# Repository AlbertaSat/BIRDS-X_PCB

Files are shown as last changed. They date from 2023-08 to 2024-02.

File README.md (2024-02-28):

# JASPER BIRDS-X PCB
Repository for the PCB design for the JASPER BIRDS-X project.

JASPER is a joint organization between the University of Alberta's AlbertaSat and the University of Calgary's CalgaryToSpace cubesat teams.

## Features
1. Capable of APRS (Automated Packet Reporting System) digipeat and store-and-forward modes, and periodic beaconing, for use by Amateur Radio enthusiasts.
2. Implements a radiation experiment, which compares the radiation shielding properties of shielding options.
	* Uses RADFET sensors as radiation detection sensors.
	* Uses linear CCD sensor (painted black) to sense galactic cosmic rays.
3. Employs power safety systems (over-current protection, enable pins, etc.) to interface with the BIRDS-X satellite parent system.
4. Uses <300 mW on receive, and <1750 mW on transmit.
5. ~~Stores data in flash memory.~~
6. Interfaces with the Mission Boss system via UART.
7. A test fixture board makes flashing and debugging the main payload board easier and more reliable.

## System Block Diagram

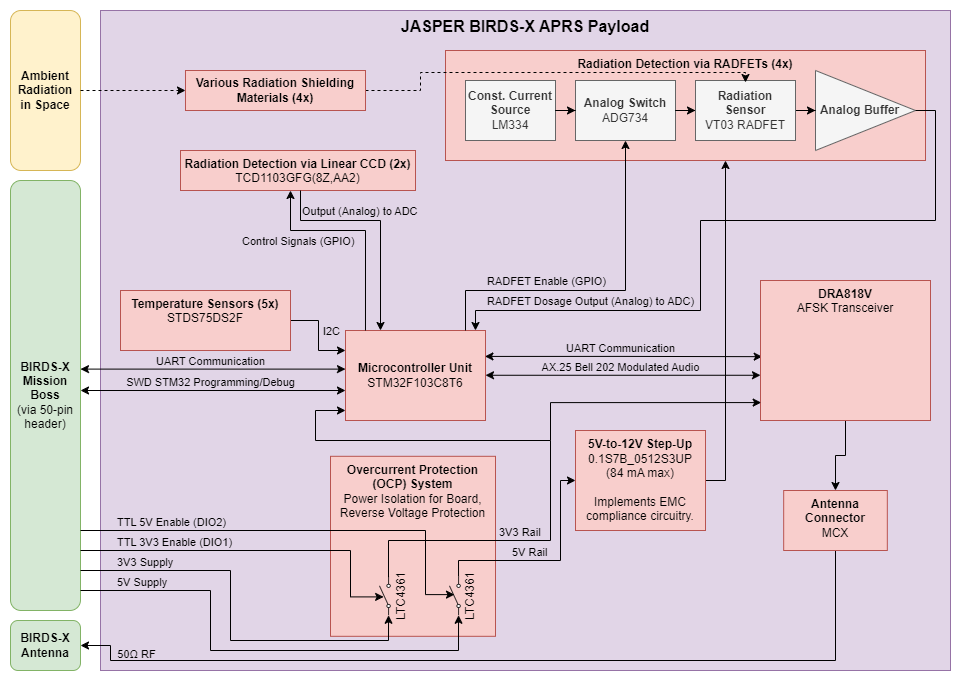
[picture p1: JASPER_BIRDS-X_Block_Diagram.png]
JASPER BIRDS-X Block Diagram


## Release Notes
See the [GitHub Releases](https://github.com/AlbertaSat/BIRDS-X_PCB/releases) for this repo.

## License

This repository is licensed under the "CERN Open Hardware Licence Version 2 - Permissive (CERN OHL v2 Permissive)" license. For more information, see [the choosealicense.com description of the license](https://choosealicense.com/licenses/cern-ohl-p-2.0/).

> CERN OHL v2 Permissive
> A permissive license for hardware designs, with conditions only requiring preservation of notices. Contributors provide an express grant of patent rights. Licensed works, modifications, and larger works may be distributed under different terms and without sources.

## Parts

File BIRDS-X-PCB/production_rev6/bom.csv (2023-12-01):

Designator | Footprint | Quantity | Value | LCSC Part #
C201, C202, C601, C701 | 0603 | 4 | 10u
C203, C204 | 0603 | 2 | 1u
C205, C206, C302 | 0603 | 3 | 4.7u
C208 | 0603 | 1 | 2.2u
C301, C303, C304, C305, C401, C402, C404, C405, C406, C407, C501, C502, C503, C504, C505 | 0603 | 15 | 100n
C403 | 0603 | 1 | 10n
C602, C603, C702, C703 | 0603 | 4 | 0.1u
C604, C605, C704, C705 | 0603 | 4 | 0.01u
D201, D202, D203, D301, D304, D_RX301, D_TX301 | 0603 | 7 | LED | C93128
D302, D303 | 0603 | 2 | LED | C375577
D801, D802, D901, D902 | D_DO-35_SOD27_P7.62mm_Horizontal | 4 | 1N457
H101, H102, H103, H104 | MountingHole_3.8mm | 4 | MountingHole
H105 | AlbertaSat_Logo_25x20mm | 1 | Logo
H106 | CTS_Logo_50x25mm | 1 | Logo
IC601, IC701 | TCD1103GFG8ZAA2 | 2 | TCD1103GFG_8Z,AA2_
J101, J102, J103 | Laird_Technologies_BMI-S-101_13.66x12.70mm | 3 | RFShield_OnePiece
J104 | PinHeader_2x25_P2.00mm_Horizontal | 1 | LPC-50M2LG
J401 | SMA_Amphenol_901-143_Horizontal_Modified | 1 | 60611002111501
JP201 | SolderJumper-2_P1.3mm_Open_RoundedPad1.0x1.5mm | 1 | Jumper_2_Open
L201 | 0603 | 1 | 6.8uH
Q201, Q202 | SOT-23 | 2 | 2N7002 | C3290044
Q203, Q204 | SOT-23 | 2 | AO3420
Q401 | SOT-23 | 1 | BC847 | C475630
Q601, Q701 | SOT-23 | 2 | 2SA1015 | C5189099
R201, R202, R802, R804, R902, R904 | 0603 | 6 | 110k
R203 | 1206 | 1 | 0.51 | C104948
R204 | 1206 | 1 | 0.075 | C171394
R205, R501, R502 | 0603 | 3 | 3k3
R206 | 0603 | 1 | 5.1k
R207 | 0603 | 1 | 51k
R301, R302, R305, R306, R309, R310, R602, R702 | 0603 | 8 | 2k2
R401, R404 | 0603 | 2 | 470
R402 | 0603 | 1 | 10k
R403, R805, R806, R807, R808, R905, R906, R907, R908 | 0603 | 9 | 0
R405, R408 | 1206 | 2 | 10k
R407, R410, R411 | 0603 | 3 | 100k
R412 | 0603 | 1 | 22k
R601, R603, R701, R703 | 0603 | 4 | 150
R801, R803, R901, R903 | 0603 | 4 | 11k
R809, R811, R909, R911 | 0603 | 4 | 10M
R810, R812, R910, R912 | 0603 | 4 | 3.6M
TP201, TP202 | TestPoint_Pad_D1.5mm | 2 | TestPoint
U201, U202 | TSOT-23-8_HandSoldering | 2 | LTC4361-2
U203 | Converter_DCDC_Gaptec_0.1S7B_3UP_THT | 1 | 0.1S7B_0512S3UP
U301 | LQFP-48_7x7mm_P0.5mm | 1 | STM32F103C8Tx | C8734
U401 | DORJI_DRA818V | 1 | DRA818V
U501, U502, U503, U504, U505 | MSOP-8_3x3mm_P0.65mm | 5 | STDS75DS2F | C283289
U601, U701 | SOIC-14_3.9x8.7mm_P1.27mm | 2 | 74HC04 | C86613
U801, U802, U901, U902 | SOIC-8_3.9x4.9mm_P1.27mm | 4 | LM334M | C140388
U803, U903 | MSOP-10_3x3mm_P0.5mm | 2 | ADG884xRM | C143911
U804, U805, U904, U905 | SOT-23-6_Handsoldering | 4 | VT03
U806, U906 | SOIC-8_3.9x4.9mm_P1.27mm | 2 | TL972IDR | C46127

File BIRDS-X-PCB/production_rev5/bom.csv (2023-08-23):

Designator | Footprint | Quantity | Value | LCSC Part #
C1101, C1102, C1103, C1104, C1105, C401, C402, C405, C408, C409, C410, C501, C502, C503, C506, C507, C512, C601, C605, C611, C701, C703, C706, C801, C803, C806, C901, C903, C906 | 0603 | 29 | 100n
C201, C202 | 0603 | 2 | 10u
C203, C205, C403, C406 | 0603 | 4 | 4.7u
C204 | 0603 | 1 | 2.2u
C206 | 1812 | 1 | 1n | C524544
C207, C208 | 0603 | 2 | 1u
C404, C407, C411, C412 | 0603 | 4 | 20p
C504 | 0603 | 1 | 10n
C603, C607, C702, C704, C802, C804, C902, C904 | 1206 | 8 | 100u
C608, C613, C705, C707, C805, C807, C905, C907 | 0603 | 8 | 47p
D201, D202, D203, D401, D_PB3, D_RX1, D_TX1 | 0603 | 7 | LED
D301, D302, D303, D304 | D_DO-35_SOD27_P7.62mm_Horizontal | 4 | 1N457
D601, D701, D801, D901 | Osram_DIL2_4.3x4.65mm_P5.08mm | 4 | BPW34
H101, H102, H103, H104 | MountingHole_3.8mm | 4 | MountingHole
H105 | AlbertaSat_Logo_25x20mm | 1 | Logo
H106 | CTS_Logo_50x25mm | 1 | Logo
J101 | PinHeader_2x25_P2.00mm_Horizontal | 1 | LPC-50M2LG
J102, J103, J104 | Laird_Technologies_BMI-S-101_13.66x12.70mm | 3 | RFShield_OnePiece
J201, J202, J203, J403 | PinHeader_1x02_P1.27mm_Vertical | 4 | Conn_01x02
J501 | SMA_Amphenol_901-143_Horizontal_Modified | 1 | 60611002111501
JP101, JP502 | SolderJumper-3_P1.3mm_Open_RoundedPad1.0x1.5mm_NumberLabels | 2 | Jumper_3_Bridged12
JP201, JP501 | SolderJumper-2_P1.3mm_Open_RoundedPad1.0x1.5mm | 2 | Jumper_2_Open
JP301 | PinHeader_1x02_P1.27mm_Vertical | 1 | Jumper_2_Open
JP401, JP402 | SolderJumper-3_P1.3mm_Open_RoundedPad1.0x1.5mm_NumberLabels | 2 | Jumper_3_Open
L201 | 0603 | 1 | 6.8uH
Q201, Q202 | SOT-23 | 2 | AO3420
Q203, Q204 | SOT-23 | 2 | 2N7002 | C3290044
Q501 | SOT-23 | 1 | BC847 | C475630
Q601, Q701, Q801, Q901 | SOT-23 | 4 | MMBF4392LT1G
R201 | 1206 | 1 | 0.51 | C104948
R202 | 1206 | 1 | 0.075 | C171394
R203 | 0603 | 1 | 1k
R204 | 0603 | 1 | 2.2k
R205, R408, R409, R513, R612, R618, R707, R710, R807, R810, R907, R910 | 0603 | 12 | 10k
R206, R207, R303, R313, R315, R317 | 0603 | 6 | 110k
R302, R312, R314, R316 | 0603 | 4 | 11k
R304, R306, R308, R310, R601, R602, R701, R702, R801, R802, R901, R902 | 0603 | 12 | 10M
R305, R307, R309, R311 | 0603 | 4 | 3.6M
R401, R402, R404, R405 | 0603 | 4 | 3.3k
R403, R406, R407, R410, R511, R512 | 0603 | 6 | 2k2
R411, R605, R703, R803, R903 | 0603 | 5 | 1M
R501, R502 | 0603 | 2 | 470
R503, R507, R508 | 0603 | 3 | 100k
R504, R505, R509, R510 | 1206 | 4 | 10k
R506 | 0603 | 1 | 22k
R607, R704, R804, R904 | 0603 | 4 | 4k7
R609, R705, R805, R905 | 0603 | 4 | 2k
R611, R617, R706, R709, R806, R809, R906, R909 | 0603 | 8 | 330k
R615, R708, R808, R908 | 0603 | 4 | 100R
SW401 | SW_Tactile_SPST_NO_Straight_CK_PTS636Sx25SMTRLFS | 1 | SW_Push
TP201, TP202, TP302, TP303, TP304 | TestPoint_Pad_D1.5mm | 5 | TestPoint
U1101, U1102, U1103, U1104, U1105 | MSOP-8_3x3mm_P0.65mm | 5 | STDS75DS2F | C283289
U201, U202 | TSOT-23-8_HandSoldering | 2 | LTC4361-2
U203 | Converter_DCDC_Gaptec_0.1S7B_3UP_THT | 1 | 0.1S7B_0512S3UP
U301, U302, U303, U304 | SOT-23-6_Handsoldering | 4 | VT03
U305 | TSSOP-14_4.4x5mm_P0.65mm | 1 | TL974IPWR
U306 | TSSOP-20_4.4x6.5mm_P0.65mm | 1 | ADG734
U308, U309, U310, U311 | SOIC-8_3.9x4.9mm_P1.27mm | 4 | LM334M | C140388
U402 | LQFP-48_7x7mm_P0.5mm | 1 | STM32F103C8Tx | C8734
U403 | U-PDFN-8_6x8mm_P1.27mm | 1 | MT29F2G01ABAGDWB-IT-G_TR | C410863
U503 | DORJI_DRA818V | 1 | DRA818V
U601, U701, U801, U901 | SOIC-8_3.9x4.9mm_P1.27mm | 4 | LM358DR | LM358DR
Y401 | Crystal_SMD_HC49-SD | 1 | 8MHz | C2842263
Y402 | Crystal_SMD_HC49-SD | 1 | 32.768 kHz | C2975358

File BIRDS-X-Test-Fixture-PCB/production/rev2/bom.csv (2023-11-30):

Designator | Footprint | Quantity | Value | LCSC Part #
C101 | 1206 | 1 | 100n
D_3V3, D_5V0 | 1206 | 2 | LED
H1, H2, H3, H4 | MountingHole_4mm_Pad | 4 | MountingHole
H_3V3_1, H_3V3_DUT_1, H_5V_1, H_5V_DUT_1, H_GND_1, H_GND_2, H_GND_3 | EdgeAlligatorConnector | 7 | MountingHole_Pad
J101 | PinHeader_2x25_P2.00mm_Horizontal | 1 | LPC-50M2LG
J102, J109 | PinHeader_1x05_P2.54mm_Vertical | 2 | Conn_01x05
J103, J104 | PinHeader_2x25_P2.54mm_Vertical | 2 | ~
J105 | PinHeader_1x06_P2.54mm_Vertical | 1 | Conn_01x06
J110, J111 | IDC-Header_2x05_P2.54mm_Latch_Vertical | 2 | Conn_02x05_Odd_Even
JP101 | PinHeader_1x03_P2.54mm_Vertical | 1 | Jumper_3_Open
JP102, JP103, JP104, JP105 | SolderJumper-2_P1.3mm_Open_RoundedPad1.0x1.5mm | 4 | SolderJumper_2_Open
JP_3V_SENSE_1, JP_5V_SENSE_1 | PinHeader_1x02_P2.54mm_Vertical | 2 | Jumper_2_Bridged
J_3V3_1, J_3V3_2, J_5V_1, J_5V_2 | TerminalBlock_bornier-2_P5.08mm | 4 | Screw_Terminal_01x02
R101, R102, R_3V3 | R_Axial_DIN0411_L9.9mm_D3.6mm_P12.70mm_Horizontal | 3 | 1k
R_5V0 | R_Axial_DIN0411_L9.9mm_D3.6mm_P12.70mm_Horizontal | 1 | 2.2k
SW_3V3_EN_DIO1, SW_5V_EN_DIO2 | SW_Slide_1P2T_CK_OS102011MS2Q | 2 | SW_SPDT
SW_RST1 | SW_PUSH_6mm | 1 | SW_Push

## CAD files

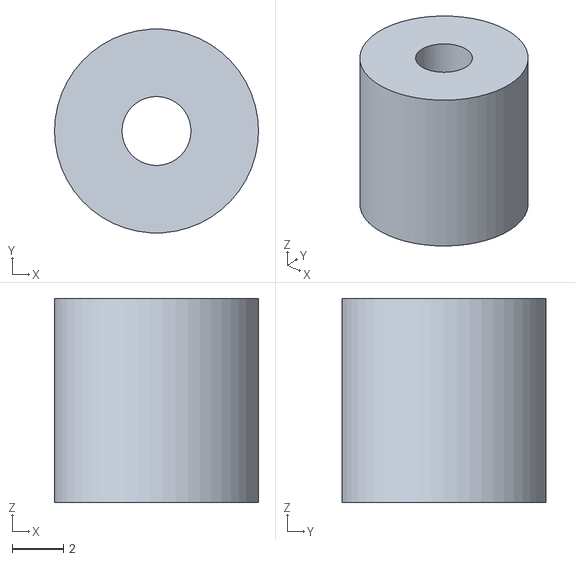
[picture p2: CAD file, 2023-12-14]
BIRDS-X-Test-Fixture-PCB/standoff_3d_print/pcb_stand_off.stl
8.00 x 7.98 x 8.00

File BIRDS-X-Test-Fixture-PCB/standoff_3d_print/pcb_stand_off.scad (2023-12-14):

$fn=50;
difference() {
    cylinder(d=8, h=8);
    cylinder(d=2.7, h=100);
}

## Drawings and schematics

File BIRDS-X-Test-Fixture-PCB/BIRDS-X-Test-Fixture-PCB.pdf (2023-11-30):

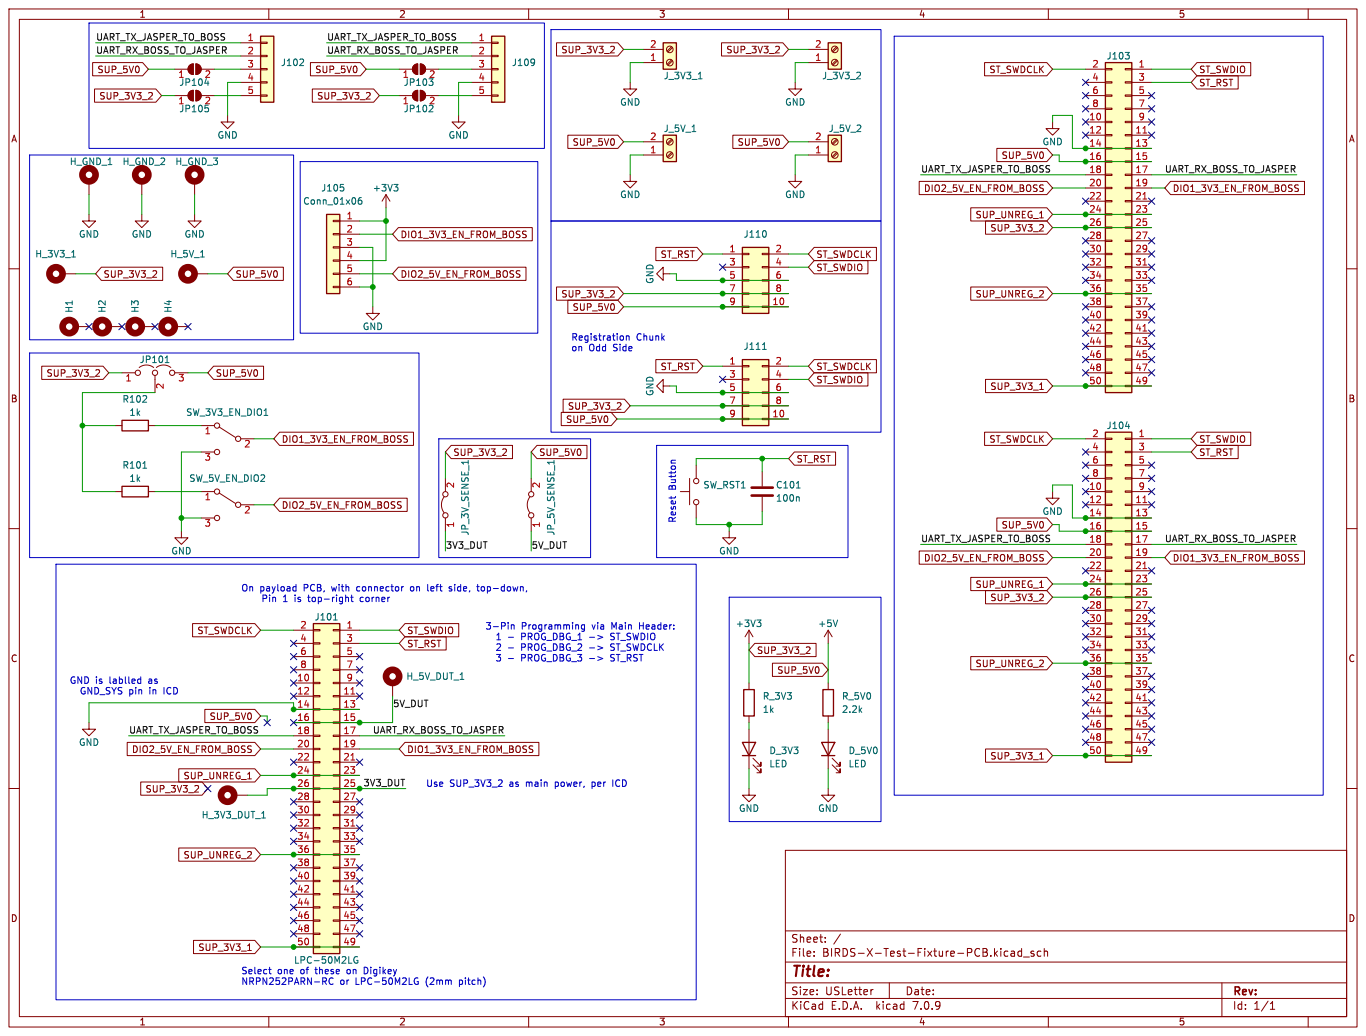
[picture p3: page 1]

Id: 1/1 Title: File: BIRDS-X-Test-Fixture-PCB.kicad_sch Sheet: /

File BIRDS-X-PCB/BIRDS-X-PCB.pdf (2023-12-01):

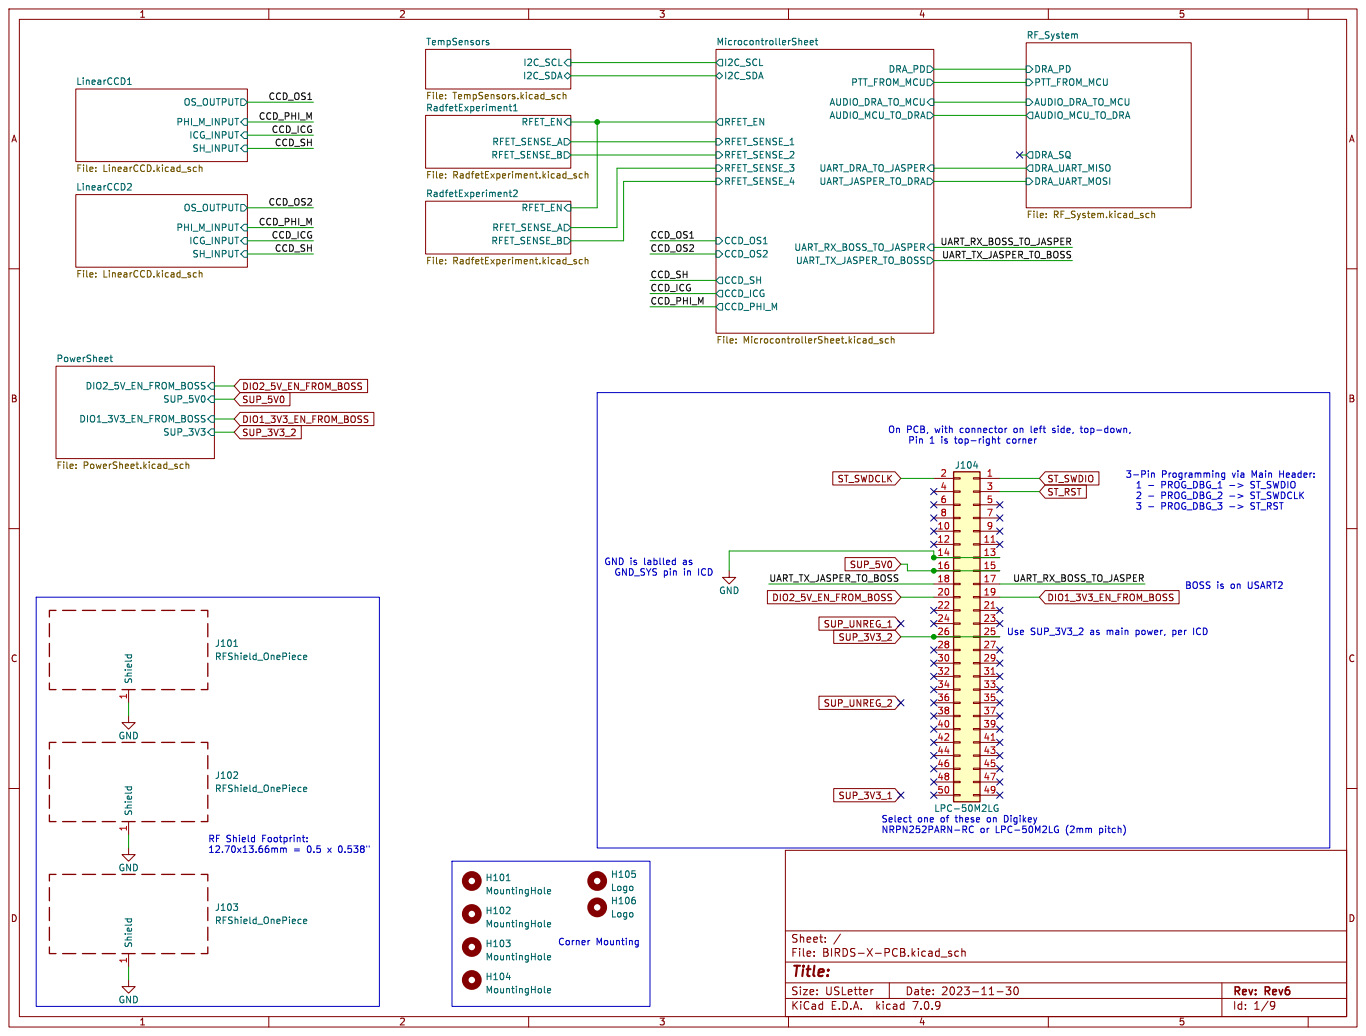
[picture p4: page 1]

LinearCCD1 File: LinearCCD.kicad_sch DIO2_5V_EN_FROM_BOSS
SUP_3V3 PowerSheet File: PowerSheet.kicad_sch Shield

Logo H103 MountingHole H102 MountingHole H101 MountingHole H104 MountingHole GNDShield

Id: 1/9 Title: File: BIRDS-X-PCB.kicad_sch Sheet: /

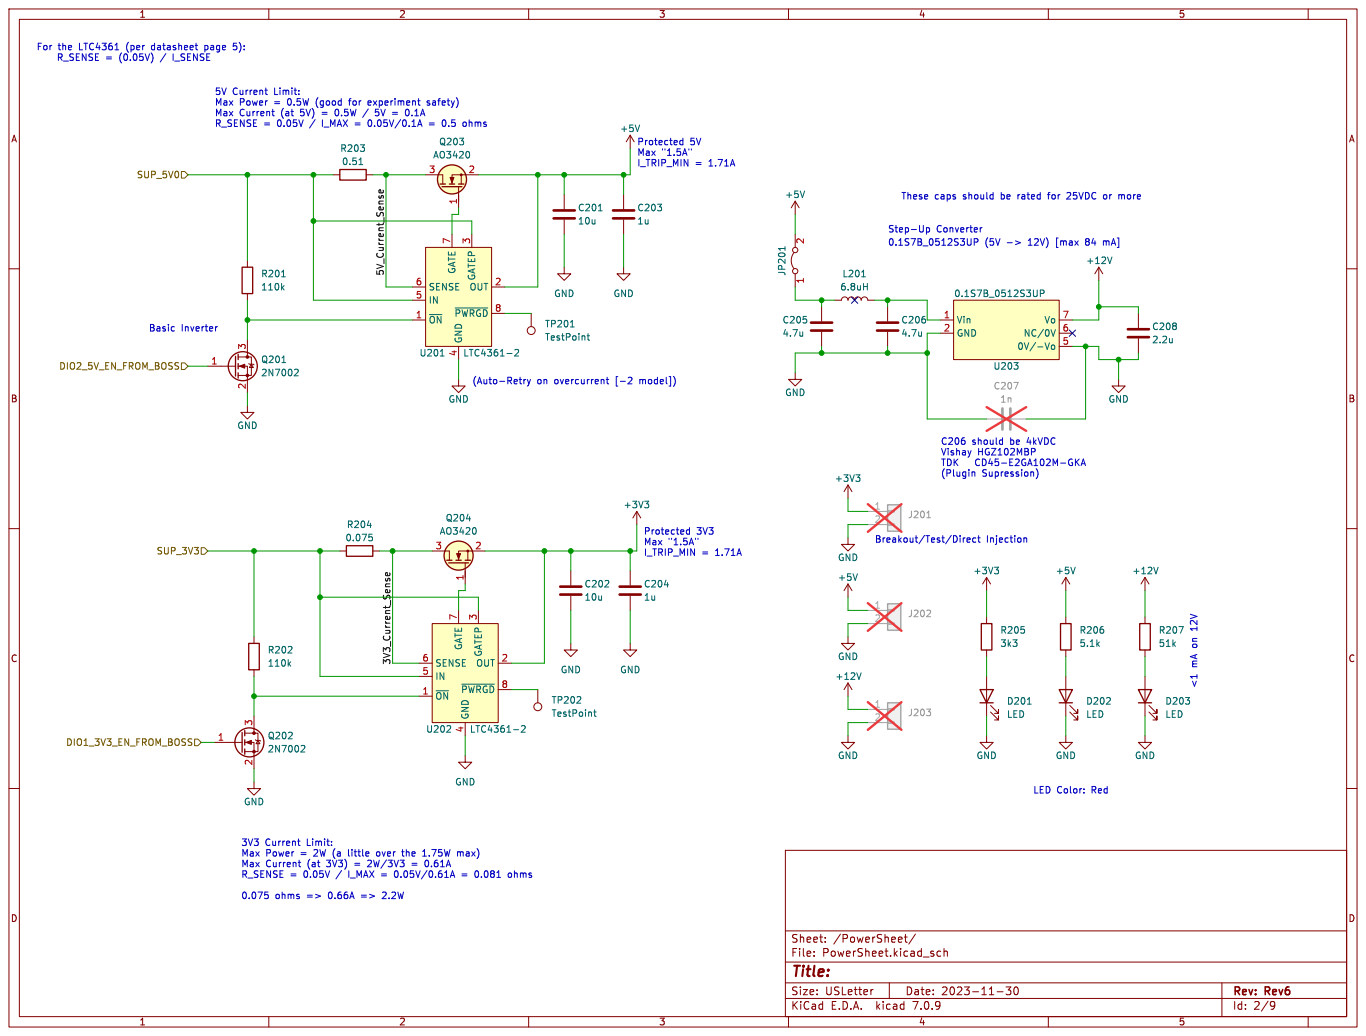
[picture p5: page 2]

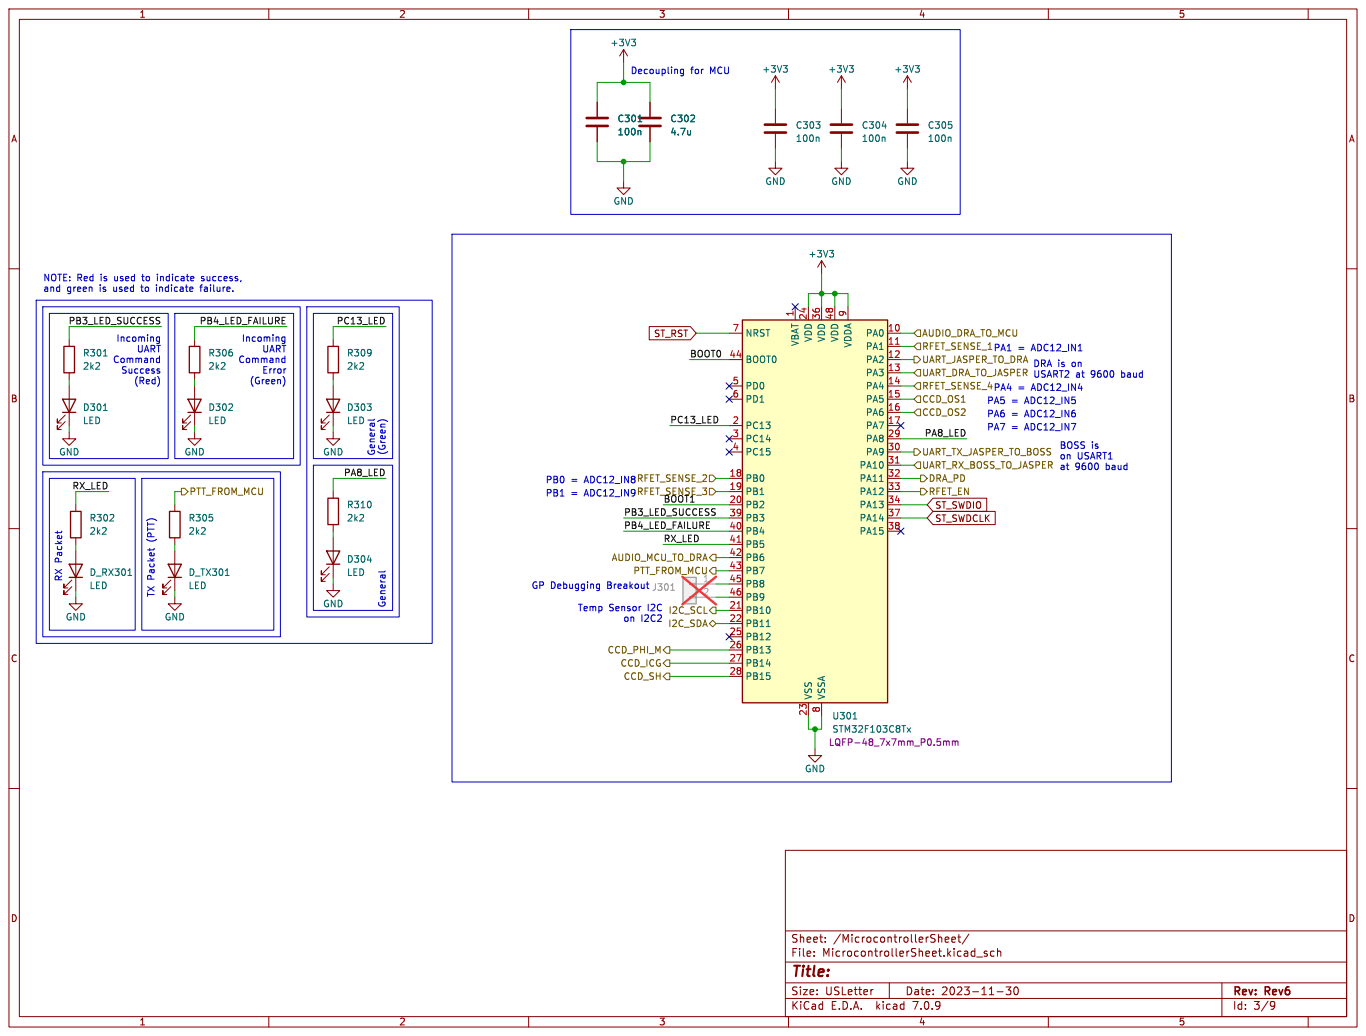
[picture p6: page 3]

1 PA0 10 PA1 11 PA2 12 PA3 13 PA4 14 PA5 15 PA6 16 PA7 17 PB0 18 PB1 19 PC13 2 PB2 20 PB10 21 PB11 22 VSS 23 VDD 24 PB12 25 PB13 26 PB14 27 PB15 28 PA8 29 PC14 3 PA9 30 PA10 31 PA11 32 PA12 33 PA13 34 VDD 36 PA14 37 PA15 38 PB3 39 PC15 4 PB4 40 PB5 41 PB6 42 PB7 43 BOOT0 44 PB8 45 PB9 46 VDD 48 PD0 5 PD1 6 NRST 7 VSSA

Incoming UART Command Success

at 9600 baud PA1 = ADC12_IN1 PA5 = ADC12_IN5 PA6 = ADC12_IN6 PA7 = ADC12_IN7 TX Packet (PTT)

Incoming UART Command Error

DRA is on USART2 at 9600 baud

Id: 3/9 Title: File: MicrocontrollerSheet.kicad_sch Sheet: /MicrocontrollerSheet/ GND

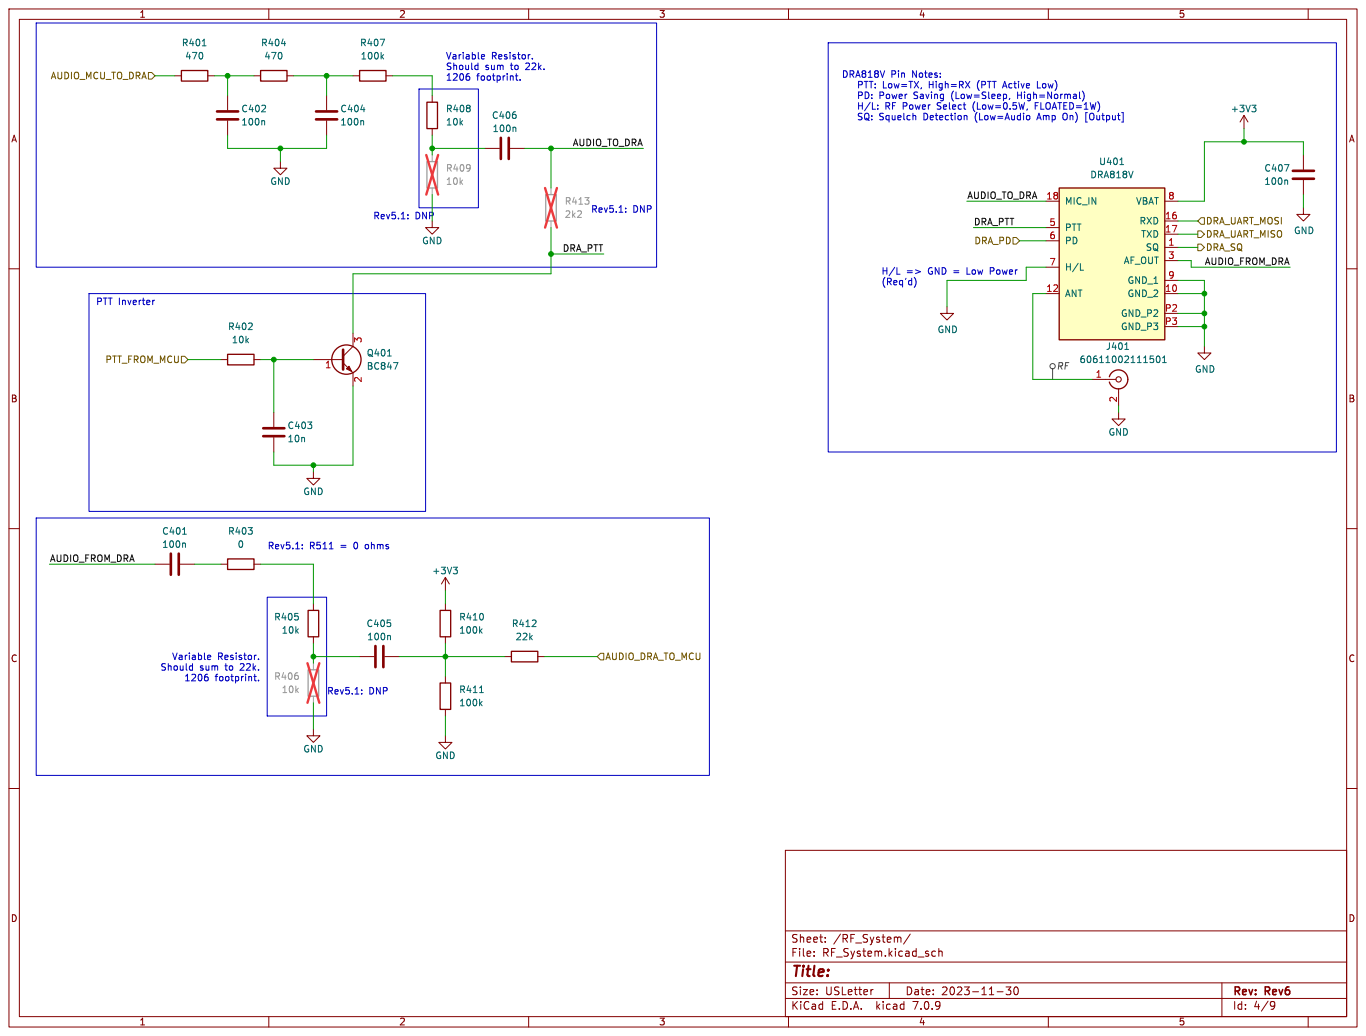
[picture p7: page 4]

Variable Resistor. Should sum to 22k. 1206 footprint.

Id: 4/9 Title: File: RF_System.kicad_sch Sheet: /RF_System/

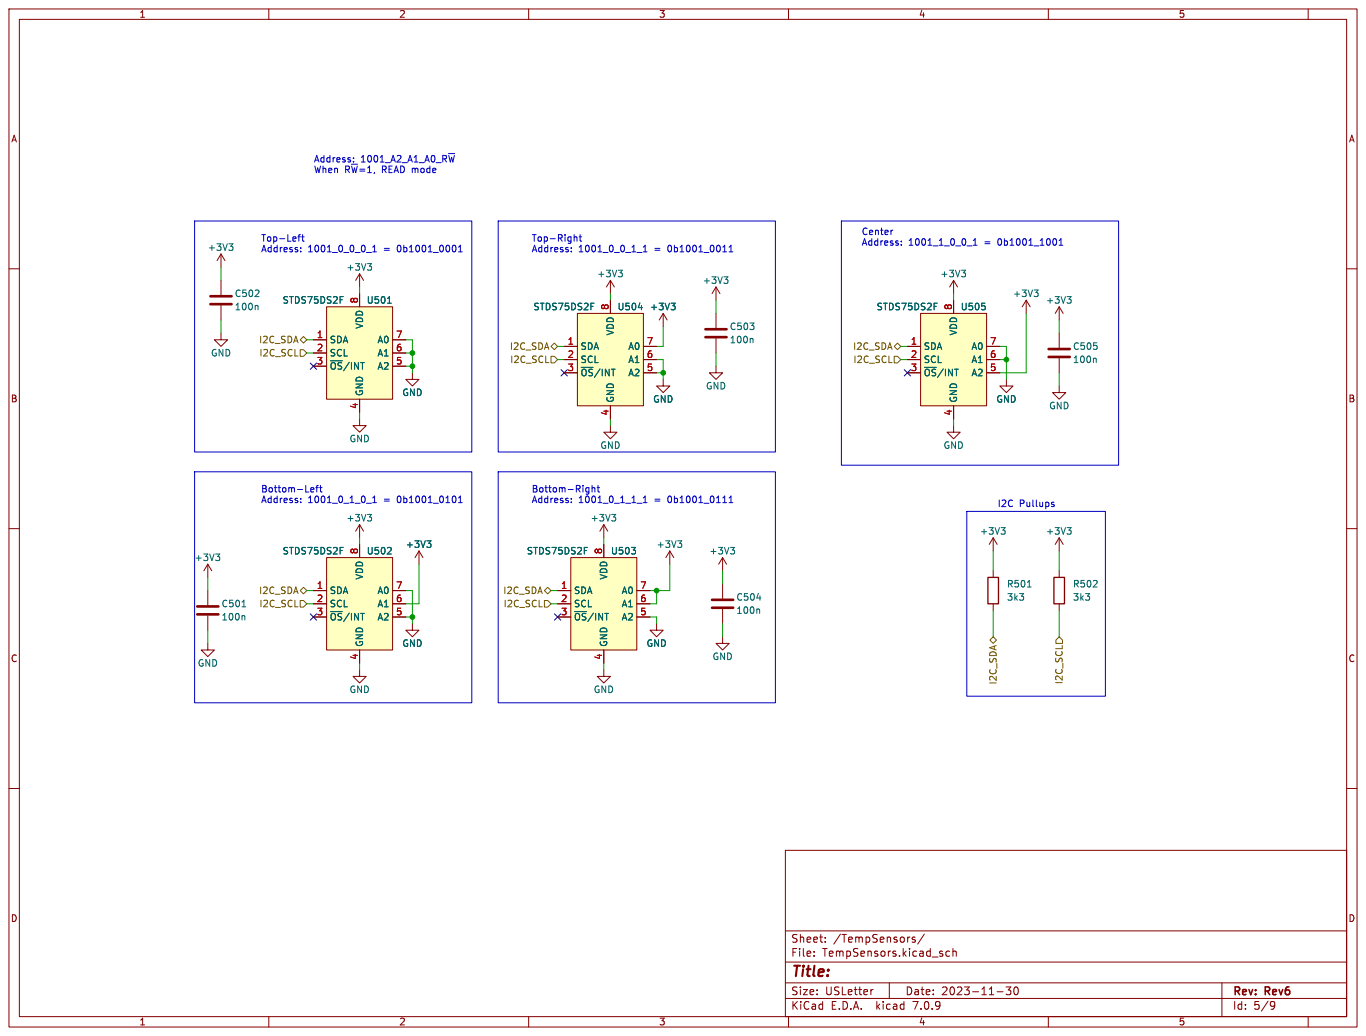
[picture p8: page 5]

8 STDS75DS2F U504 SDA 1 SCL 2 ~{OS}/INT 3 GND

Id: 5/9 Title: File: TempSensors.kicad_sch Sheet: /TempSensors/ GND

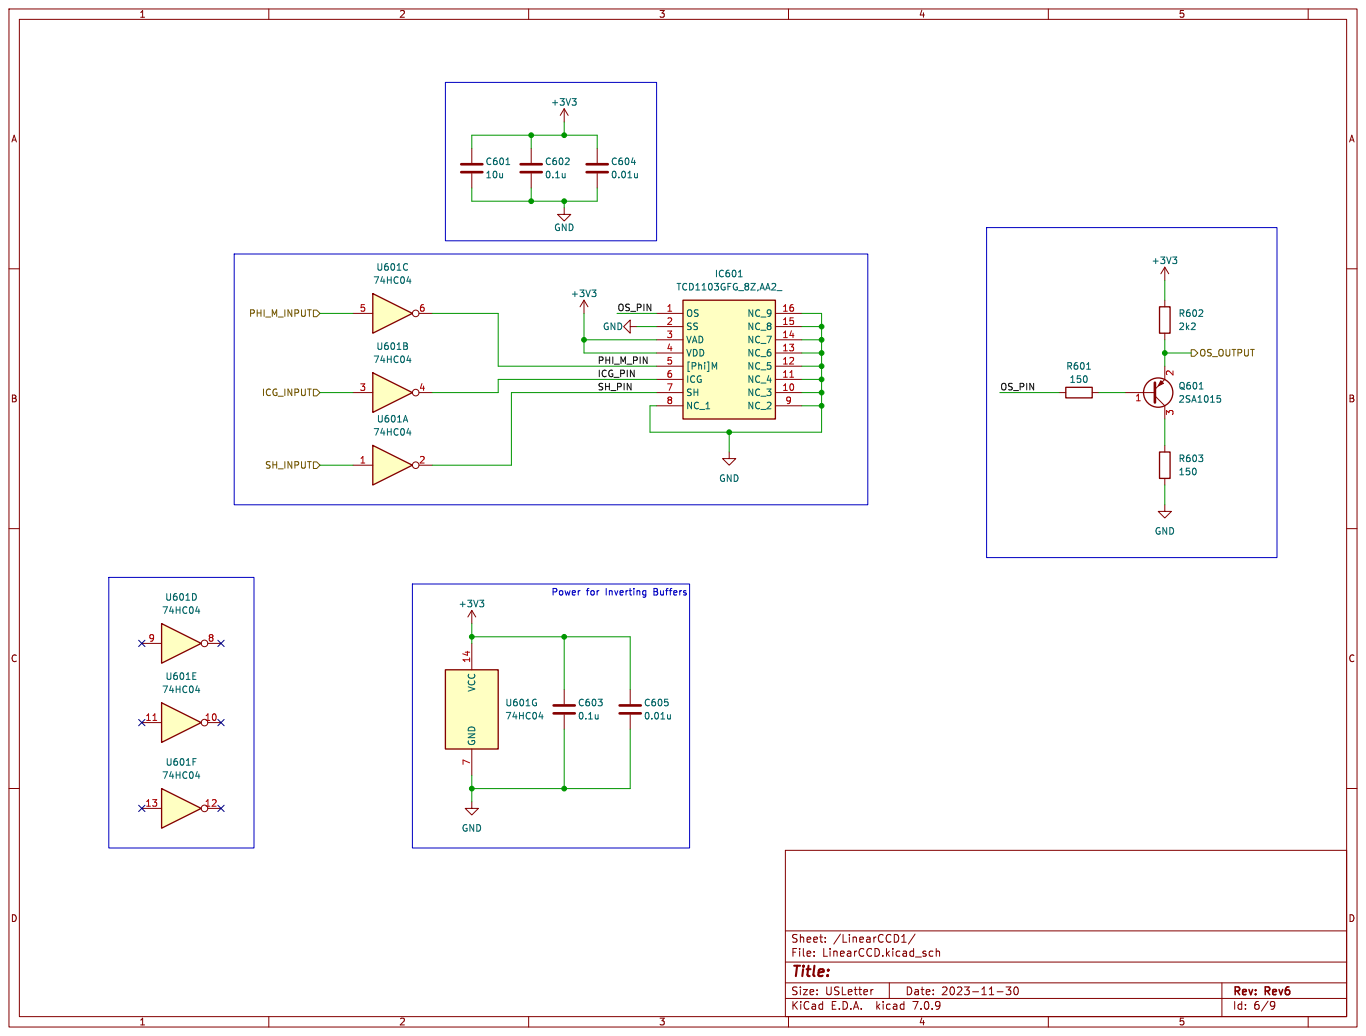
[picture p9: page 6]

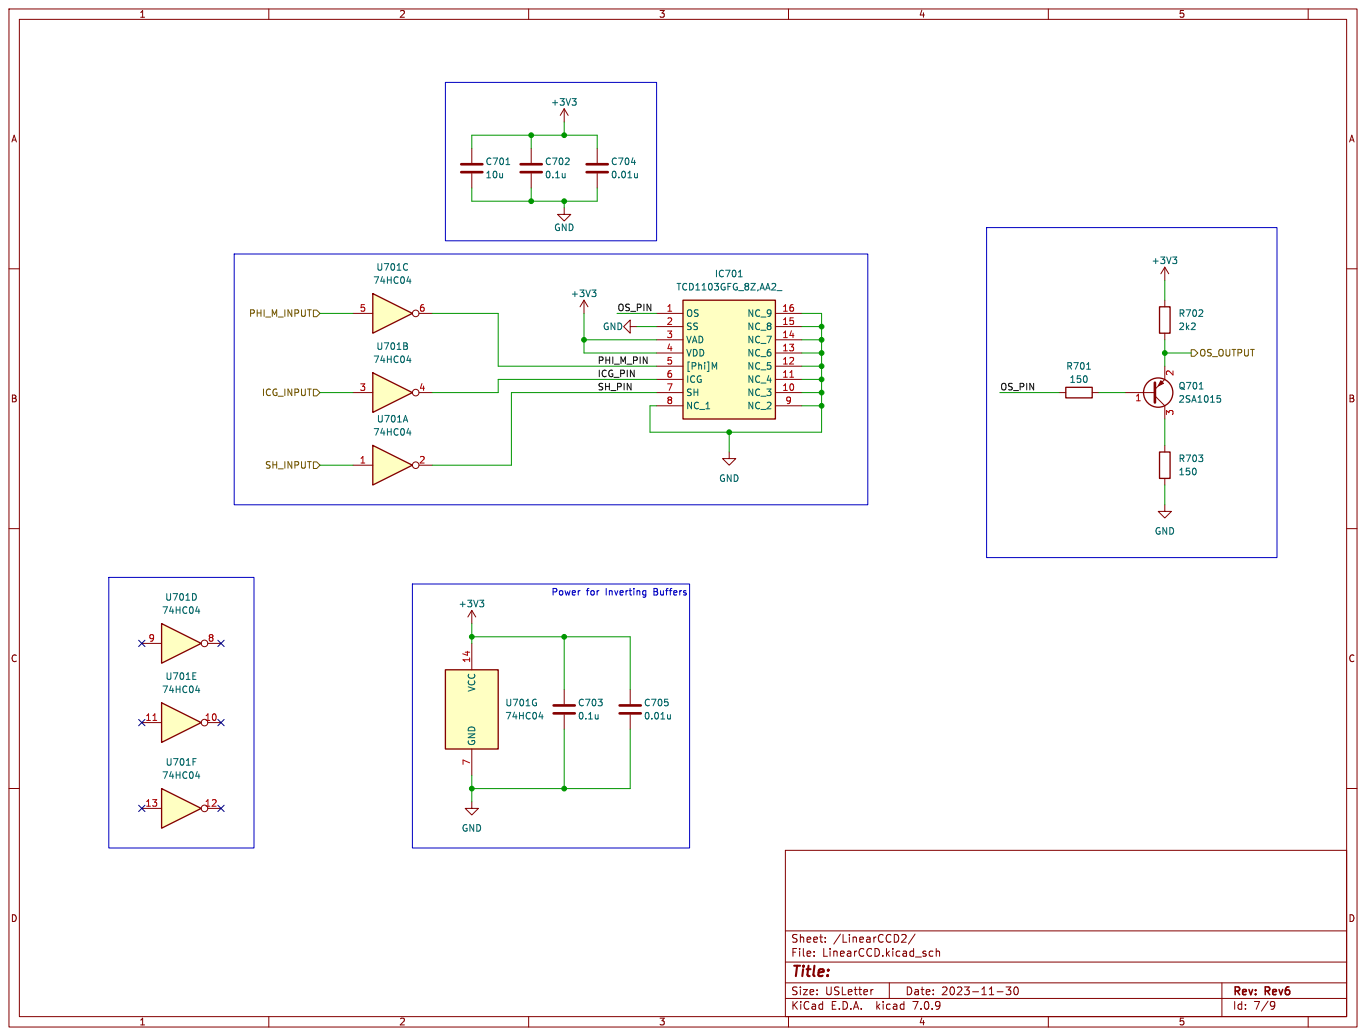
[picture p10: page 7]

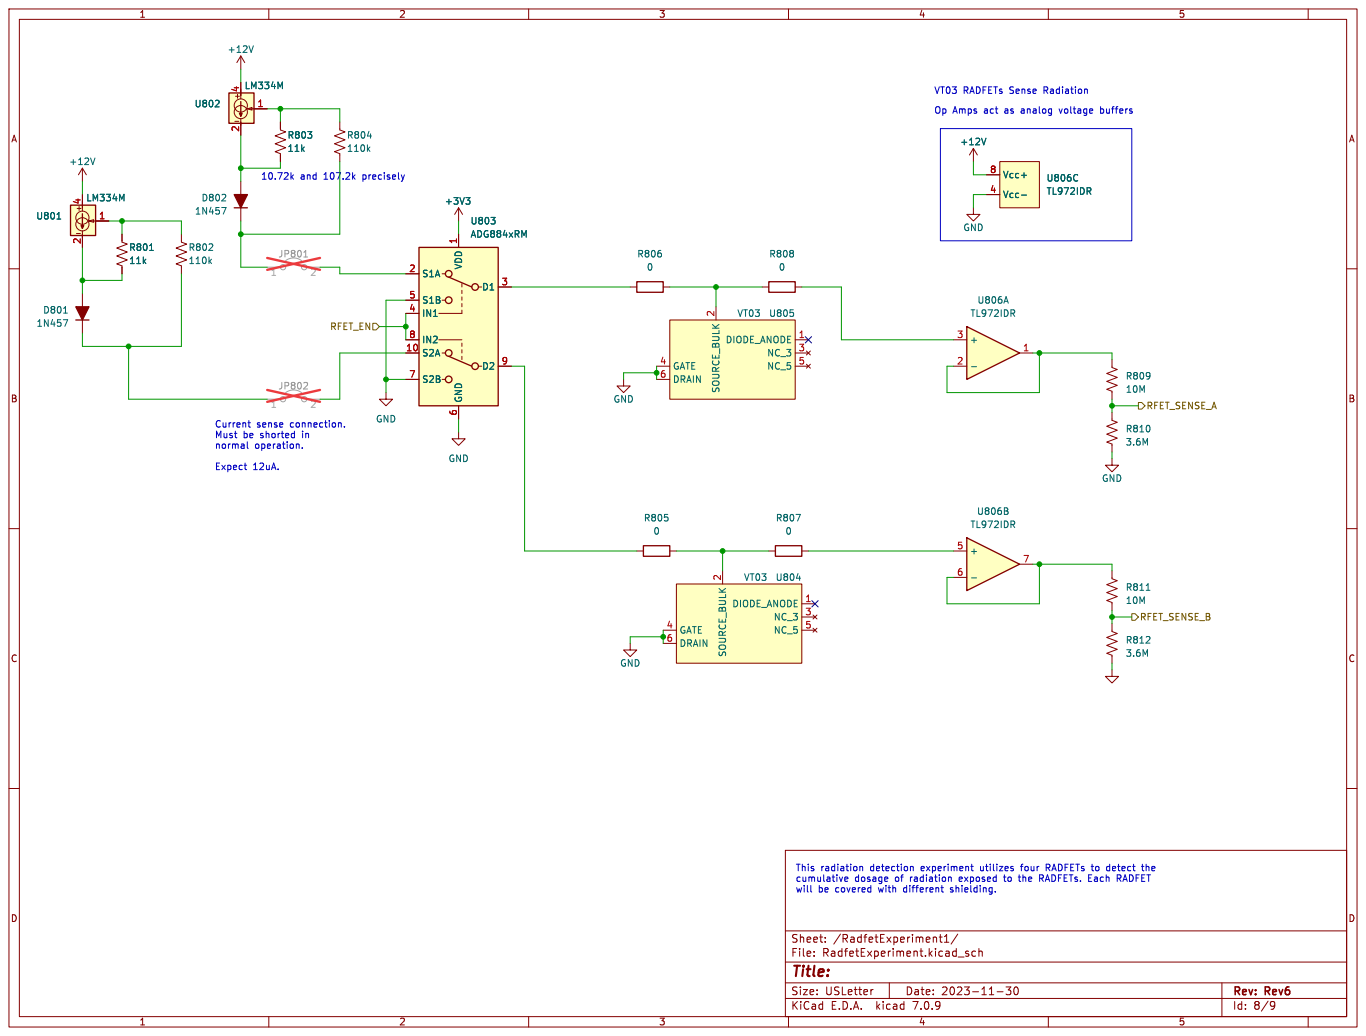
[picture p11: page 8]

Id: 8/9 Title: File: RadfetExperiment.kicad_sch Sheet: /RadfetExperiment1/

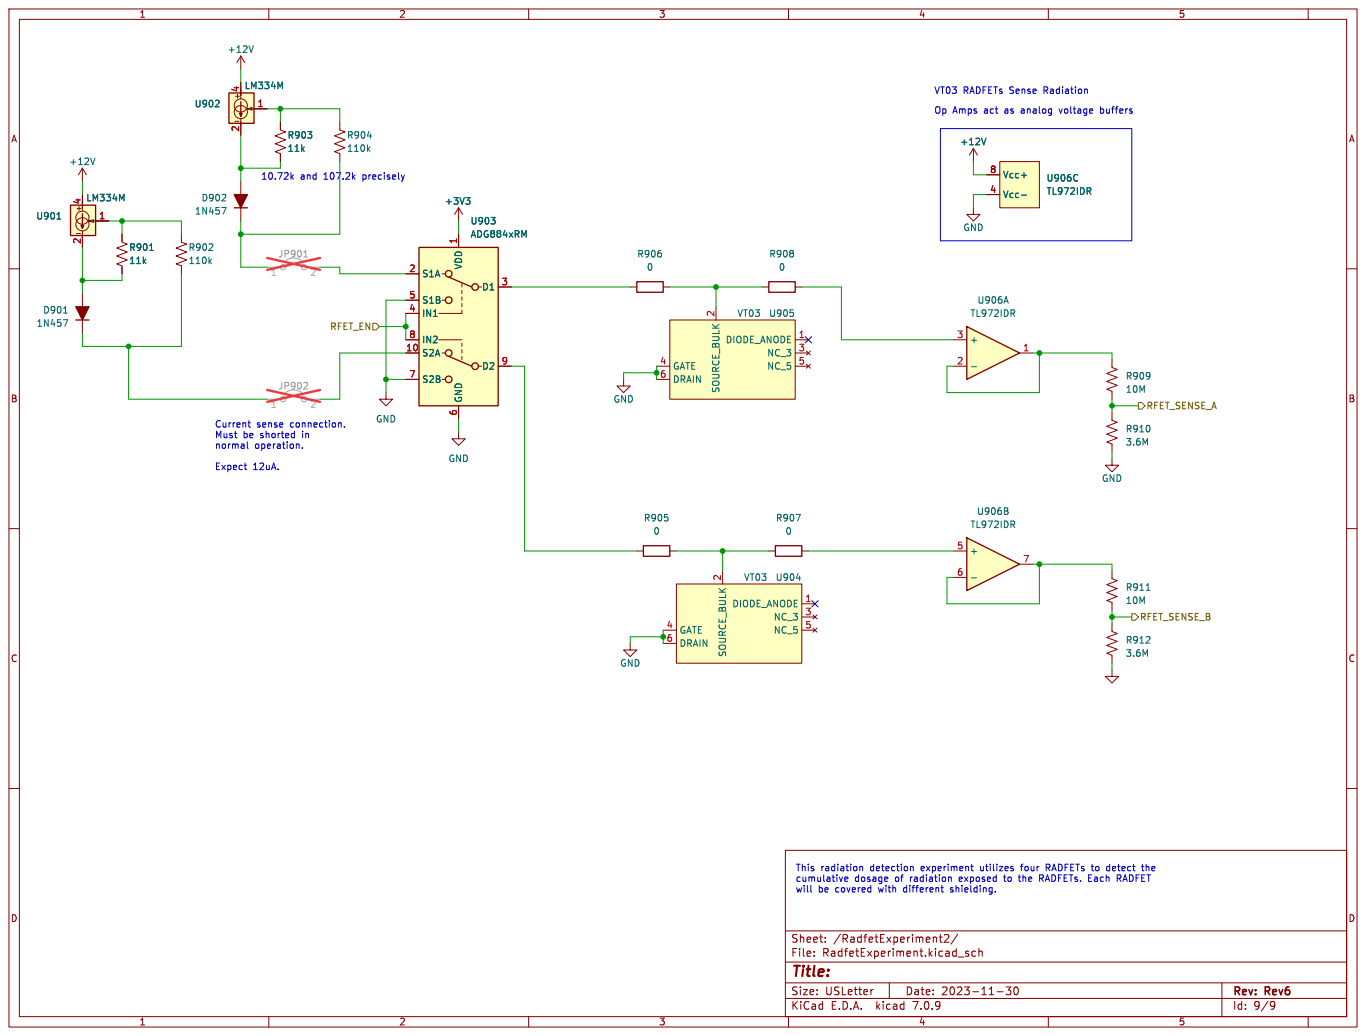
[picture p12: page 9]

Id: 9/9 Title: File: RadfetExperiment.kicad_sch Sheet: /RadfetExperiment2/

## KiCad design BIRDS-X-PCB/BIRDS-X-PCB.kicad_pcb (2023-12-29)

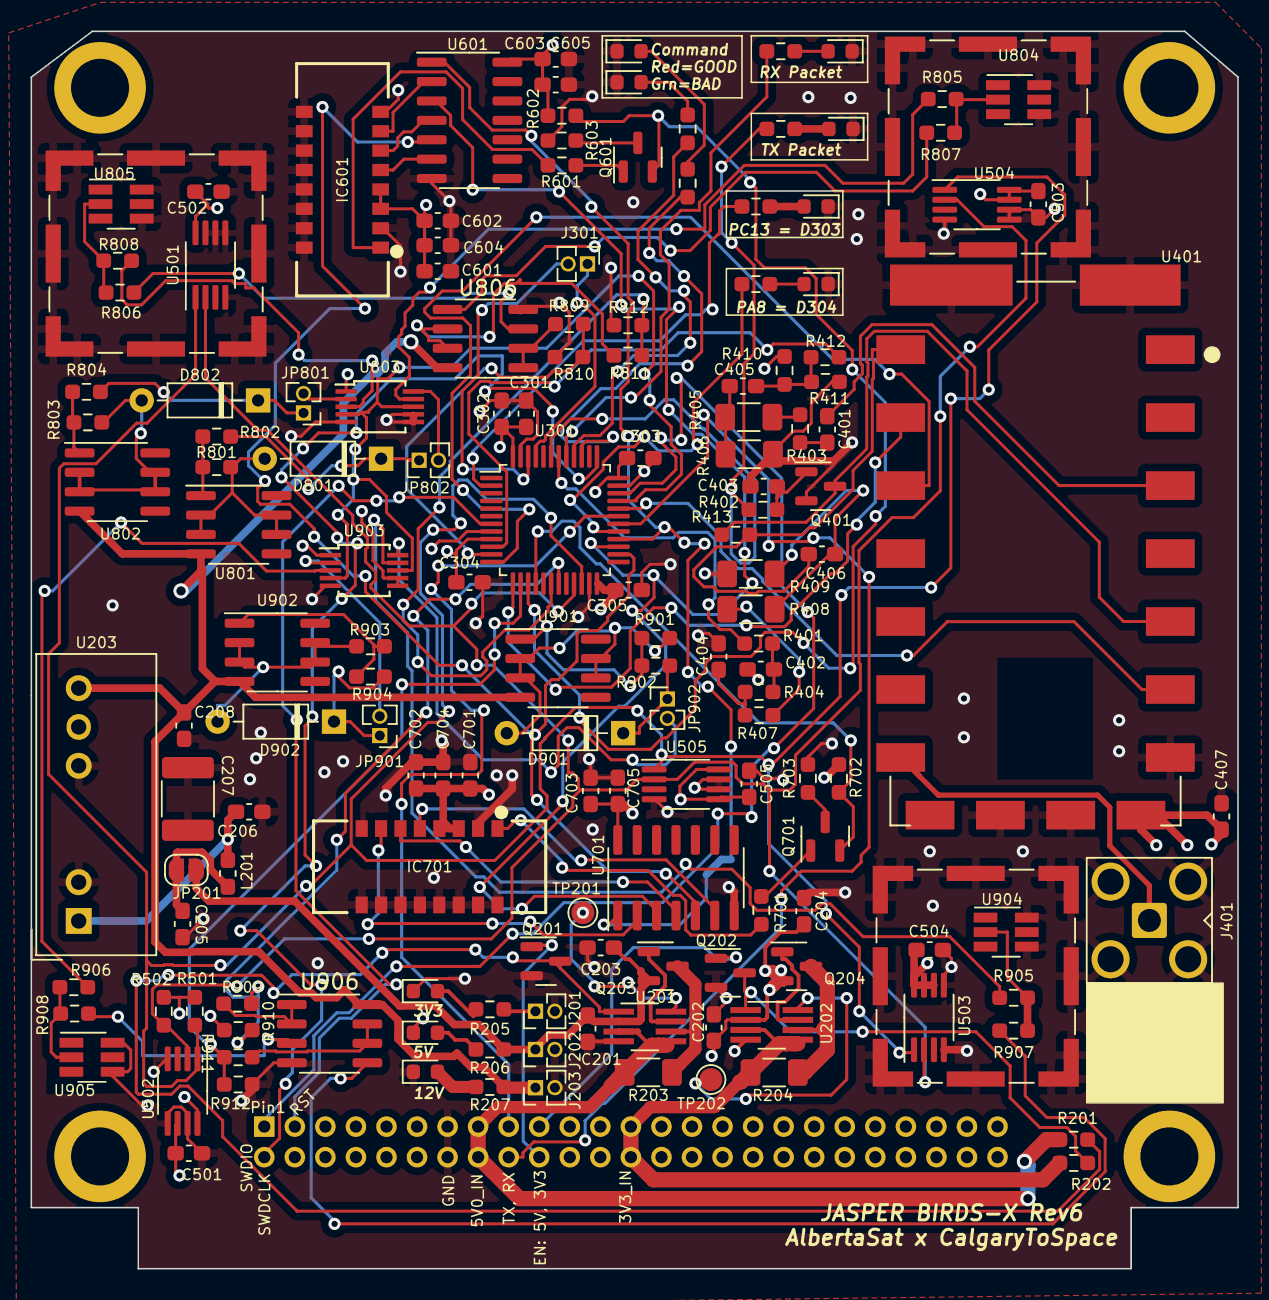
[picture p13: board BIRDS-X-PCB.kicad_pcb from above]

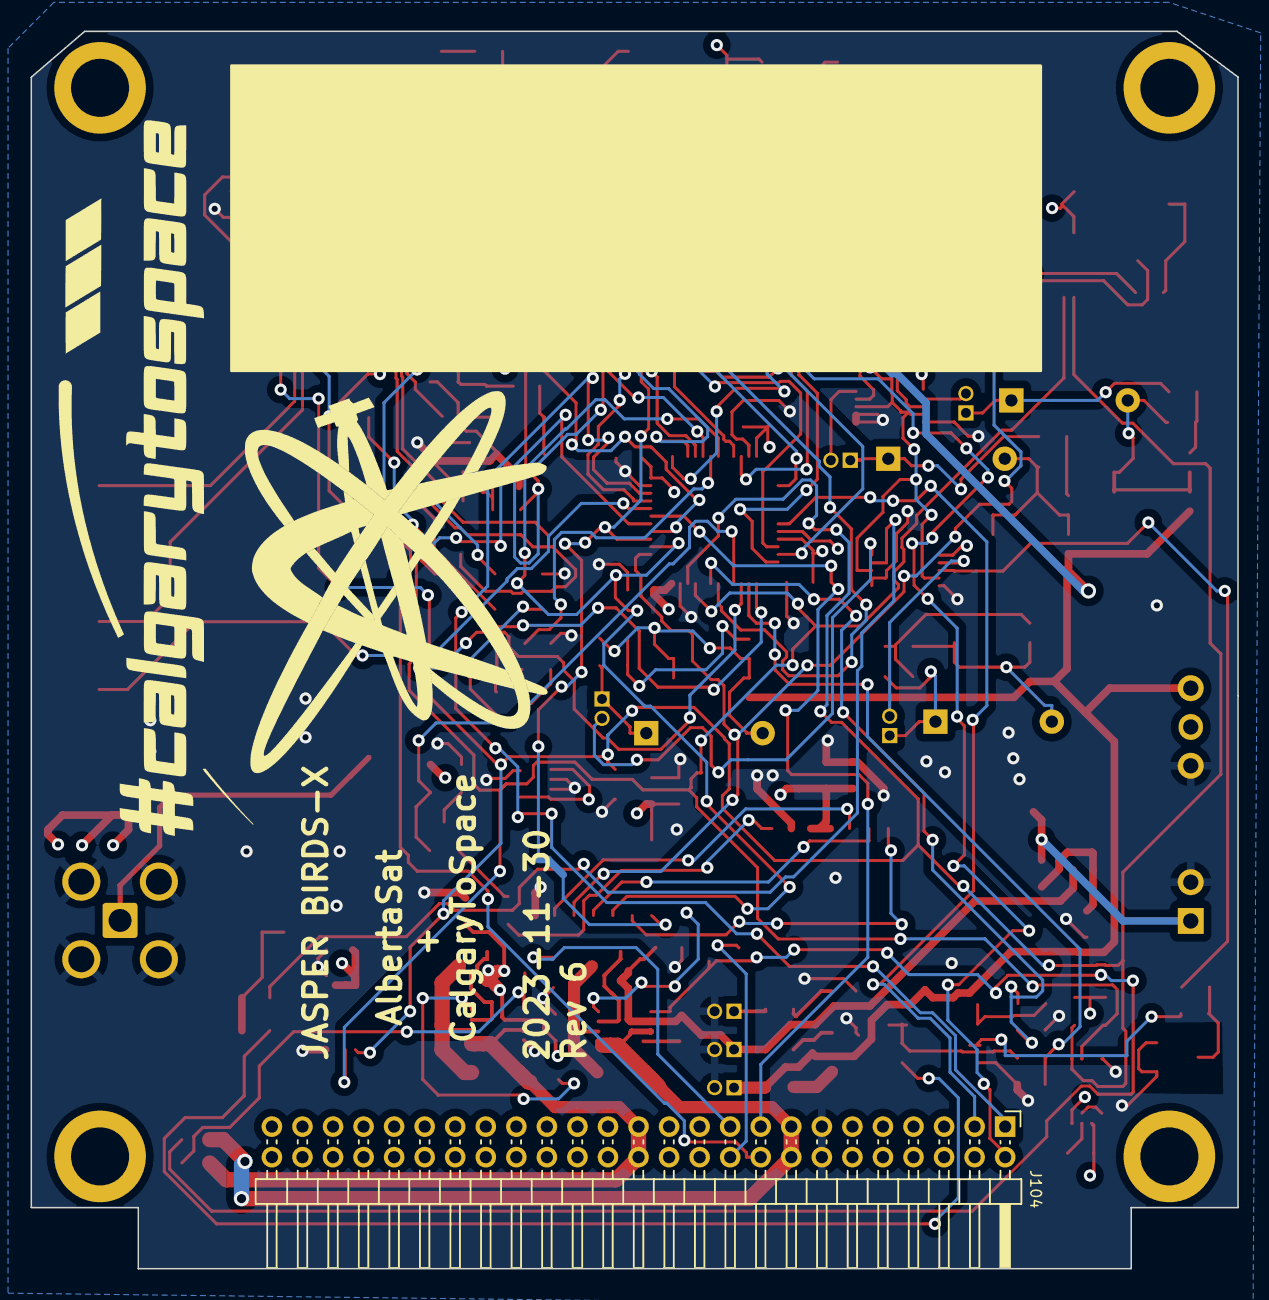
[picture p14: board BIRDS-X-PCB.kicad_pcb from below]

Board: 4 copper layers, 79.0 x 81.0 mm, 162 parts (3 on the bottom side), 114 nets.

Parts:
C201, C202, C601, C701: 10u; C_0603_1608Metric_Pad1.08x0.95mm_HandSolder
C203, C204: 1u; C_0603_1608Metric_Pad1.08x0.95mm_HandSolder
C205, C206, C302: 4.7u; C_0603_1608Metric_Pad1.08x0.95mm_HandSolder
C207: 1n; C_1812_4532Metric
C208: 2.2u; C_0603_1608Metric_Pad1.08x0.95mm_HandSolder
C301, C303, C304, C305, C401, C402, C404, C405, C406, C407, C501, C502, C503, C504, C505: 100n; C_0603_1608Metric_Pad1.08x0.95mm_HandSolder
C403: 10n; C_0603_1608Metric_Pad1.08x0.95mm_HandSolder
C602, C603, C702, C703: 0.1u; C_0603_1608Metric_Pad1.08x0.95mm_HandSolder
C604, C605, C704, C705: 0.01u; C_0603_1608Metric_Pad1.08x0.95mm_HandSolder
D201, D202, D203, D301, D302, D303, D304: LED; LED_0603_1608Metric
D801, D802, D901, D902: 1N457; D_DO-35_SOD27_P7.62mm_Horizontal
D_RX301: LED; LED_0603_1608Metric
D_TX301: LED; LED_0603_1608Metric
H101, H102, H103, H104: MountingHole; MountingHole_3.8mm
H105: Logo; AlbertaSat_Logo_25x20mm
H106: Logo; CTS_Logo_50x25mm
IC601, IC701: TCD1103GFG_8Z,AA2_; TCD1103GFG8ZAA2
J101, J102, J103: RFShield_OnePiece; Laird_Technologies_BMI-S-101_13.66x12.70mm
J104: LPC-50M2LG; PinHeader_2x25_P2.00mm_Horizontal
J201, J202, J203, J301: Conn_01x02; PinHeader_1x02_P1.27mm_Vertical
J401: 60611002111501; SMA_Amphenol_901-143_Horizontal_Modified
JP201: Jumper_2_Open; SolderJumper-2_P1.3mm_Open_RoundedPad1.0x1.5mm
JP801, JP802, JP901, JP902: Jumper_2_Open; PinHeader_1x02_P1.27mm_Vertical
L201: 6.8uH; L_0603_1608Metric_Pad1.05x0.95mm_HandSolder
Q201, Q202: 2N7002; SOT-23
Q203, Q204: AO3420; SOT-23
Q401: BC847; SOT-23
Q601, Q701: 2SA1015; SOT-23
R201, R202, R802, R804, R902, R904: 110k; R_0603_1608Metric_Pad0.98x0.95mm_HandSolder
R203: 0.51; R_1206_3216Metric_Pad1.30x1.75mm_HandSolder
R204: 0.075; R_1206_3216Metric_Pad1.30x1.75mm_HandSolder
R205, R501, R502: 3k3; R_0603_1608Metric_Pad0.98x0.95mm_HandSolder
R206: 5.1k; R_0603_1608Metric_Pad0.98x0.95mm_HandSolder
R207: 51k; R_0603_1608Metric_Pad0.98x0.95mm_HandSolder
R301, R302, R305, R306, R309, R310, R413, R602, R702: 2k2; R_0603_1608Metric_Pad0.98x0.95mm_HandSolder
R401, R404: 470; R_0603_1608Metric_Pad0.98x0.95mm_HandSolder
R402: 10k; R_0603_1608Metric_Pad0.98x0.95mm_HandSolder
R403, R805, R806, R807, R808, R905, R906, R907, R908: 0; R_0603_1608Metric_Pad0.98x0.95mm_HandSolder
R405, R406, R408, R409: 10k; R_1206_3216Metric_Pad1.30x1.75mm_HandSolder
R407, R410, R411: 100k; R_0603_1608Metric_Pad0.98x0.95mm_HandSolder
R412: 22k; R_0603_1608Metric_Pad0.98x0.95mm_HandSolder
R601, R603, R701, R703: 150; R_0603_1608Metric_Pad0.98x0.95mm_HandSolder
R801, R803, R901, R903: 11k; R_0603_1608Metric_Pad0.98x0.95mm_HandSolder
R809, R811, R909, R911: 10M; R_0603_1608Metric_Pad0.98x0.95mm_HandSolder
R810, R812, R910, R912: 3.6M; R_0603_1608Metric_Pad0.98x0.95mm_HandSolder
TP201, TP202: TestPoint; TestPoint_Pad_D1.5mm
U201, U202: LTC4361-2; TSOT-23-8_HandSoldering
U203: 0.1S7B_0512S3UP; Converter_DCDC_Gaptec_0.1S7B_3UP_THT
U301: STM32F103C8Tx; LQFP-48_7x7mm_P0.5mm
U401: DRA818V; DORJI_DRA818V
U501, U502, U503, U504, U505: STDS75DS2F; MSOP-8_3x3mm_P0.65mm
U601, U701: 74HC04; SOIC-14_3.9x8.7mm_P1.27mm
U801, U802, U901, U902: LM334M; SOIC-8_3.9x4.9mm_P1.27mm
U803, U903: ADG884xRM; MSOP-10_3x3mm_P0.5mm
U804, U805, U904, U905: VT03; SOT-23-6_Handsoldering
U806, U906: TL972IDR; SOIC-8_3.9x4.9mm_P1.27mm

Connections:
+3V3: C202.1, C204.1, C301.1, C302.1, C303.1, C304.1, C305.1, C407.1, C501.1, C502.1, C503.1, C504.1, C505.1, C601.1, C602.1, C603.1, C604.1, C605.1, C701.1, C702.1, C703.1, C704.1, C705.1, IC601.3 (VAD), IC601.4 (VDD), IC701.3 (VAD), IC701.4 (VDD), J201.1, Q204.2 (S), R205.1, R410.1, R501.1, R502.1, R602.2, R702.2, U202.2 (OUT), U301.9 (VDDA), U301.24 (VDD), U301.36 (VDD), U301.48 (VDD), U401.8 (VBAT), U501.8 (VDD), U502.6 (A1), U502.8 (VDD), U503.6 (A1), U503.7 (A0), U503.8 (VDD), U504.7 (A0), U504.8 (VDD), U505.5 (A2), U505.8 (VDD), U601.14 (VCC), U701.14 (VCC), U803.1 (VDD), U903.1 (VDD)
+5V: C201.1, C203.1, J202.1, JP201.2 (B), Q203.2 (S), R206.1, U201.2 (OUT)
+12V: C208.1, J203.1, R207.1, U203.7 (Vo), U801.4, U802.4, U806.8 (Vcc+), U901.4, U902.4, U906.8 (Vcc+)
/CCD_ICG: U301.27 (PB14), U601.3, U701.3
/CCD_OS1: Q601.2 (E), R602.1, U301.15 (PA5)
/CCD_OS2: Q701.2 (E), R702.1, U301.16 (PA6)
/CCD_PHI_M: U301.26 (PB13), U601.5, U701.5
/CCD_SH: U301.28 (PB15), U601.1, U701.1
/LinearCCD1/ICG_PIN: IC601.6 (ICG), U601.4
/LinearCCD1/OS_PIN: IC601.1 (OS), R601.1
/LinearCCD1/PHI_M_PIN: IC601.5 ([Phi]M), U601.6
/LinearCCD1/SH_PIN: IC601.7 (SH), U601.2
/LinearCCD2/ICG_PIN: IC701.6 (ICG), U701.4
/LinearCCD2/OS_PIN: IC701.1 (OS), R701.1
/LinearCCD2/PHI_M_PIN: IC701.5 ([Phi]M), U701.6
/LinearCCD2/SH_PIN: IC701.7 (SH), U701.2
/MicrocontrollerSheet/AUDIO_DRA_TO_MCU: R412.1, U301.10 (PA0)
/MicrocontrollerSheet/AUDIO_MCU_TO_DRA: R401.1, U301.42 (PB6)
/MicrocontrollerSheet/DRA_PD: U301.32 (PA11), U401.6 (PD)
/MicrocontrollerSheet/I2C_SCL: R502.2, U301.21 (PB10), U501.2 (SCL), U502.2 (SCL), U503.2 (SCL), U504.2 (SCL), U505.2 (SCL)
/MicrocontrollerSheet/I2C_SDA: R501.2, U301.22 (PB11), U501.1 (SDA), U502.1 (SDA), U503.1 (SDA), U504.1 (SDA), U505.1 (SDA)
/MicrocontrollerSheet/PA8_LED: R310.1, U301.29 (PA8)
/MicrocontrollerSheet/PB3_LED_SUCCESS: R301.1, U301.39 (PB3)
/MicrocontrollerSheet/PB4_LED_FAILURE: R306.1, U301.40 (PB4)
/MicrocontrollerSheet/PC13_LED: R309.1, U301.2 (PC13)
/MicrocontrollerSheet/PTT_FROM_MCU: R305.1, R402.1, U301.43 (PB7)
/MicrocontrollerSheet/RFET_EN: U301.33 (PA12), U803.4 (IN1), U803.8 (IN2), U903.4 (IN1), U903.8 (IN2)
/MicrocontrollerSheet/RFET_SENSE_1: R809.2, R810.1, U301.11 (PA1)
/MicrocontrollerSheet/RFET_SENSE_2: R811.2, R812.1, U301.18 (PB0)
/MicrocontrollerSheet/RFET_SENSE_3: R909.2, R910.1, U301.19 (PB1)
/MicrocontrollerSheet/RFET_SENSE_4: R911.2, R912.1, U301.14 (PA4)
/MicrocontrollerSheet/RX_LED: R302.1, U301.41 (PB5)
/MicrocontrollerSheet/UART_DRA_TO_JASPER: U301.13 (PA3), U401.17 (TXD)
/MicrocontrollerSheet/UART_JASPER_TO_DRA: U301.12 (PA2), U401.16 (RXD)
/PowerSheet/3V3_Current_Sense: Q204.3 (D), R204.2, U202.6 (SENSE)
/PowerSheet/5V_Current_Sense: Q203.3 (D), R203.2, U201.6 (SENSE)
/RF_System/AUDIO_FROM_DRA: C401.2, U401.3 (AF_OUT)
/RF_System/AUDIO_TO_DRA: C406.2, R413.2, U401.18 (MIC_IN)
/RF_System/DRA_PTT: Q401.3 (C), R413.1, U401.5 (PTT)
/UART_RX_BOSS_TO_JASPER: J104.17, U301.31 (PA10)
/UART_TX_JASPER_TO_BOSS: J104.18, U301.30 (PA9)
DIO1_3V3_EN_FROM_BOSS: J104.19, Q202.1 (G)
DIO2_5V_EN_FROM_BOSS: J104.20, Q201.1 (G)
GND: C201.2, C202.2, C203.2, C204.2, C205.2, C206.2, C207.1, C207.2, C208.2, C301.2, C302.2, C303.2, C304.2, C305.2, C402.2, C403.2, C404.2, C407.2, C501.2, C502.2, C503.2, C504.2, C505.2, C601.2, C602.2, C603.2, C604.2, C605.2, C701.2, C702.2, C703.2, C704.2, C705.2, D201.1 (K), D202.1 (K), D203.1 (K), D301.1 (K), D302.1 (K), D303.1 (K), D304.1 (K), D_RX301.1 (K), D_TX301.1 (K), IC601.2 (SS), IC601.8 (NC_1), IC601.9 (NC_2), IC601.10 (NC_3), IC601.11 (NC_4), IC601.12 (NC_5), IC601.13 (NC_6), IC601.14 (NC_7), IC601.15 (NC_8), IC601.16 (NC_9), IC701.2 (SS), IC701.8 (NC_1), IC701.9 (NC_2), IC701.10 (NC_3), IC701.11 (NC_4), IC701.12 (NC_5), IC701.13 (NC_6), IC701.14 (NC_7), IC701.15 (NC_8), IC701.16 (NC_9), J101.1 (Shield), J102.1 (Shield), J103.1 (Shield), J104.13, J104.14, J201.2, J202.2, J203.2, J401.2 (Ext), Q201.2 (S), Q202.2 (S), Q401.2 (E), R406.1, R409.1, R411.2, R603.2, R703.2, R810.2, R812.2, R910.2, R912.2, U201.4 (GND), U202.4 (GND), U203.2 (GND), U203.5 (0V/-Vo), U301.8 (VSSA), U301.23 (VSS), U301.35 (VSS), U301.47 (VSS), U401.7 (H/L), U401.9 (GND_1), U401.10 (GND_2), U401.P2 (GND_P2), U401.P3 (GND_P3), U501.4 (GND), U501.5 (A2), U501.6 (A1), U501.7 (A0), U502.4 (GND), U502.5 (A2), U502.7 (A0), U503.4 (GND), U503.5 (A2), U504.4 (GND), U504.5 (A2), U504.6 (A1), U505.4 (GND), U505.6 (A1), U505.7 (A0), U601.7 (GND), U701.7 (GND), U803.5 (S1B), U803.6 (GND), U803.7 (S2B), U804.4 (GATE), U804.6 (DRAIN), U805.4 (GATE), U805.6 (DRAIN), U806.4 (Vcc-), U903.5 (S1B), U903.6 (GND), U903.7 (S2B), U904.4 (GATE), U904.6 (DRAIN), U905.4 (GATE), U905.6 (DRAIN), U906.4 (Vcc-)
unnamed: C401.1, R403.2
unnamed: C402.1, R401.2, R404.1
unnamed: C404.1, R404.2, R407.1
unnamed: C405.1, R405.1, R406.2
unnamed: C405.2, R410.2, R411.1, R412.2
unnamed: C406.1, R408.1, R409.2
unnamed: D201.2 (A), R205.2
unnamed: D202.2 (A), R206.2
unnamed: D203.2 (A), R207.2
unnamed: D301.2 (A), R301.2
unnamed: D302.2 (A), R306.2
unnamed: D303.2 (A), R309.2
unnamed: D304.2 (A), R310.2
unnamed: D801.2 (A), R801.2, U801.2, U801.3, U801.6, U801.7
unnamed: D801.1 (K), JP802.1 (A), R802.2
unnamed: D802.2 (A), R803.2, U802.2, U802.3, U802.6, U802.7
unnamed: D802.1 (K), JP801.1 (A), R804.2
unnamed: D901.2 (A), R901.2, U901.2, U901.3, U901.6, U901.7
unnamed: D901.1 (K), JP902.1 (A), R902.2
unnamed: D902.2 (A), R903.2, U902.2, U902.3, U902.6, U902.7
unnamed: D902.1 (K), JP901.1 (A), R904.2
unnamed: D_RX301.2 (A), R302.2
unnamed: D_TX301.2 (A), R305.2
unnamed: J301.1, U301.45 (PB8)
unnamed: J301.2, U301.46 (PB9)
unnamed: J401.1 (In), U401.12 (ANT)
unnamed: C205.1, JP201.1 (A), L201.1
unnamed: JP801.2 (B), U803.2 (S1A)
unnamed: JP802.2 (B), U803.10 (S2A)
unnamed: JP901.2 (B), U903.2 (S1A)
unnamed: JP902.2 (B), U903.10 (S2A)
unnamed: Q201.3 (D), R201.2, U201.1 (~ON)
unnamed: Q202.3 (D), R202.2, U202.1 (~ON)
unnamed: Q203.1 (G), U201.7 (GATE)
unnamed: Q204.1 (G), U202.7 (GATE)
unnamed: C403.1, Q401.1 (B), R402.2
unnamed: Q601.1 (B), R601.2
unnamed: Q601.3 (C), R603.1
unnamed: Q701.1 (B), R701.2
unnamed: Q701.3 (C), R703.1
unnamed: R403.1, R405.2
unnamed: R407.2, R408.2
unnamed: R801.1, R802.1, U801.1
unnamed: R803.1, R804.1, U802.1
unnamed: R901.1, R902.1, U901.1
unnamed: R903.1, R904.1, U902.1
unnamed: TP201.1, U201.8 (~PWRGD)
unnamed: TP202.1, U202.8 (~PWRGD)
unnamed: C206.1, L201.2, U203.1 (Vin)
unnamed: R806.1, U803.3 (D1)
unnamed: R805.1, U803.9 (D2)
unnamed: R805.2, R807.1, U804.2 (SOURCE_BULK)
unnamed: R806.2, R808.1, U805.2 (SOURCE_BULK)
unnamed: R808.2, U806.3 (+)
unnamed: R809.1, U806.1, U806.2 (-)
unnamed: R807.2, U806.5 (+)
unnamed: R811.1, U806.6 (-), U806.7
unnamed: R906.1, U903.3 (D1)
unnamed: R905.1, U903.9 (D2)
unnamed: R905.2, R907.1, U904.2 (SOURCE_BULK)
unnamed: R906.2, R908.1, U905.2 (SOURCE_BULK)
unnamed: R908.2, U906.3 (+)
unnamed: R909.1, U906.1, U906.2 (-)
unnamed: R907.2, U906.5 (+)
unnamed: R911.1, U906.6 (-), U906.7
ST_RST: J104.3, U301.7 (NRST)
ST_SWDCLK: J104.2, U301.37 (PA14)
ST_SWDIO: J104.1, U301.34 (PA13)
SUP_3V3_2: J104.25, J104.26, R202.1, R204.1, U202.3 (GATEP), U202.5 (IN)
SUP_5V0: J104.15, J104.16, R201.1, R203.1, U201.3 (GATEP), U201.5 (IN)

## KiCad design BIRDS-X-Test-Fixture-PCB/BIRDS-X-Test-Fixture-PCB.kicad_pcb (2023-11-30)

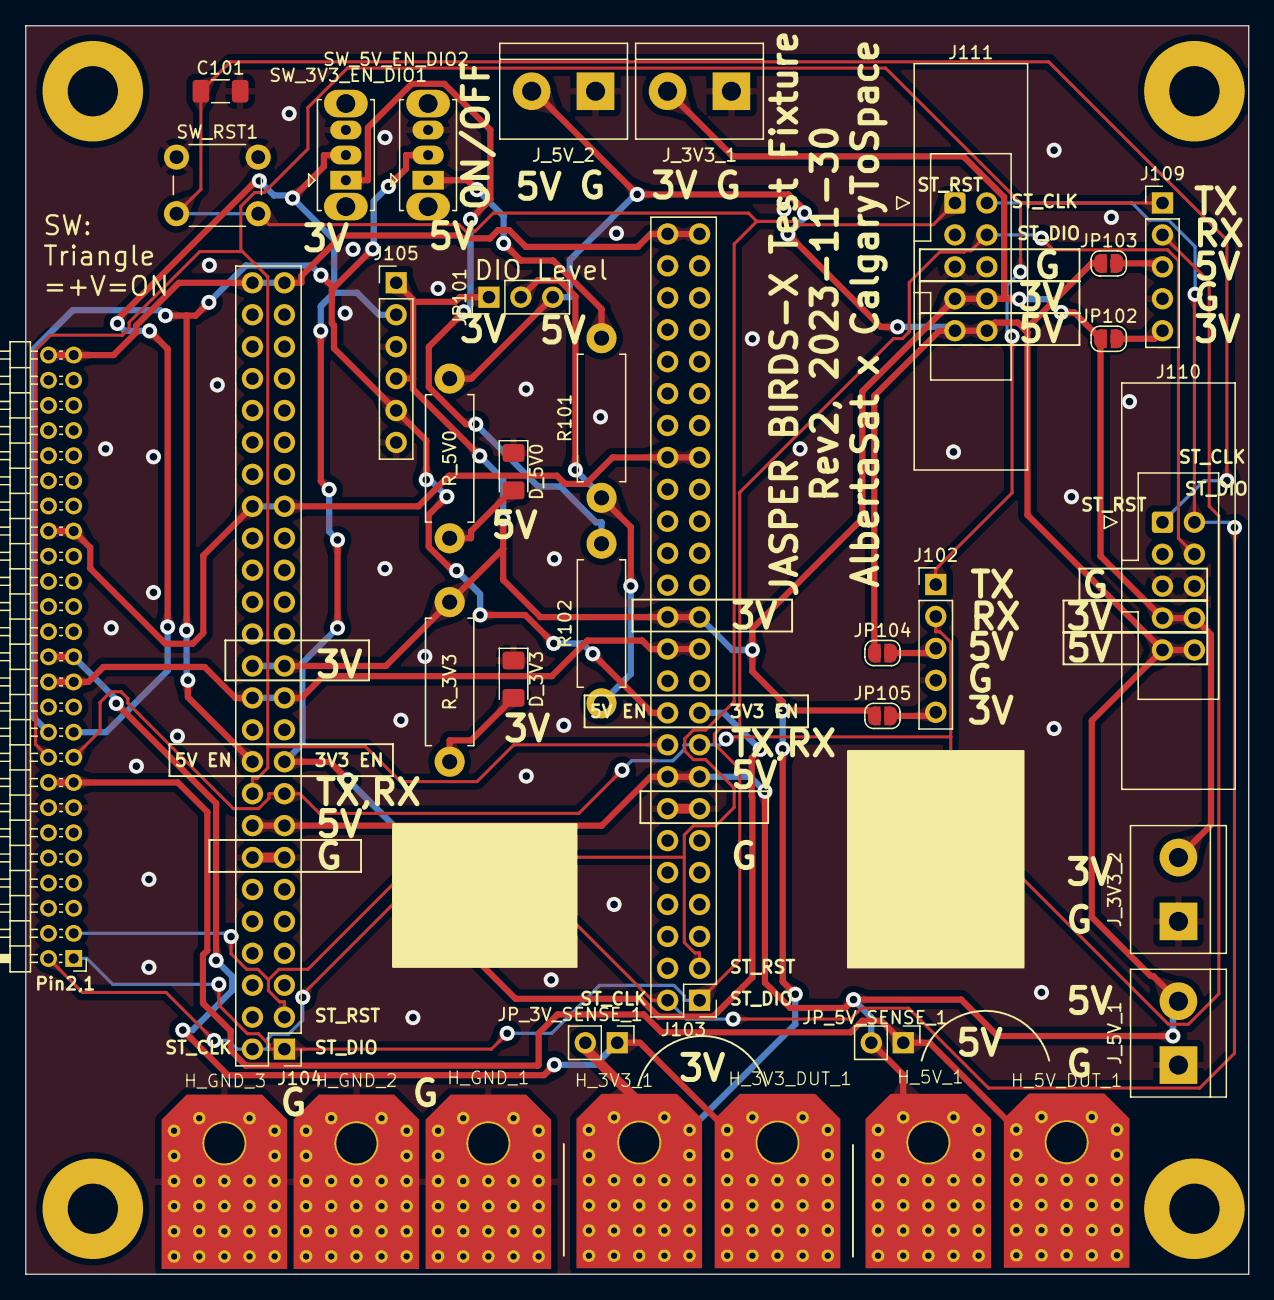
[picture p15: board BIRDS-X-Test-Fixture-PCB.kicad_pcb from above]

Board: 2 copper layers, 97.3 x 99.3 mm, 40 parts (0 on the bottom side), 24 nets.

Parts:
C101: 100n; C_1206_3216Metric_Pad1.33x1.80mm_HandSolder
D_3V3, D_5V0: LED; LED_1206_3216Metric_Pad1.42x1.75mm_HandSolder
H1, H2, H3, H4: MountingHole; MountingHole_4mm_Pad
H_3V3_1, H_3V3_DUT_1, H_5V_1, H_5V_DUT_1: MountingHole_Pad; EdgeAlligatorConnector
H_GND_1, H_GND_2, H_GND_3: MountingHole_Pad; EdgeAlligatorConnector
J101: LPC-50M2LG; PinHeader_2x25_P2.00mm_Horizontal
J102, J109: Conn_01x05; PinHeader_1x05_P2.54mm_Vertical
J103, J104: PinHeader_2x25_P2.54mm_Vertical
J105: Conn_01x06; PinHeader_1x06_P2.54mm_Vertical
J110, J111: Conn_02x05_Odd_Even; IDC-Header_2x05_P2.54mm_Latch_Vertical
JP101: Jumper_3_Open; PinHeader_1x03_P2.54mm_Vertical
JP102, JP103, JP104, JP105: SolderJumper_2_Open; SolderJumper-2_P1.3mm_Open_RoundedPad1.0x1.5mm
JP_3V_SENSE_1, JP_5V_SENSE_1: Jumper_2_Bridged; PinHeader_1x02_P2.54mm_Vertical
J_3V3_1, J_3V3_2, J_5V_1, J_5V_2: Screw_Terminal_01x02; TerminalBlock_bornier-2_P5.08mm
R101, R102: 1k; R_Axial_DIN0411_L9.9mm_D3.6mm_P12.70mm_Horizontal
R_3V3: 1k; R_Axial_DIN0411_L9.9mm_D3.6mm_P12.70mm_Horizontal
R_5V0: 2.2k; R_Axial_DIN0411_L9.9mm_D3.6mm_P12.70mm_Horizontal
SW_3V3_EN_DIO1, SW_5V_EN_DIO2: SW_SPDT; SW_Slide_1P2T_CK_OS102011MS2Q
SW_RST1: SW_Push; SW_PUSH_6mm

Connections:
/3V3_DUT: H_3V3_DUT_1.1, J101.25, J101.26, JP_3V_SENSE_1.1 (A)
/5V_DUT: H_5V_DUT_1.1, J101.15, J101.16, JP_5V_SENSE_1.1 (A)
/UART_RX_BOSS_TO_JASPER: J101.17, J102.2, J103.17, J104.17, J109.2
/UART_TX_JASPER_TO_BOSS: J101.18, J102.1, J103.18, J104.18, J109.1
DIO1_3V3_EN_FROM_BOSS: J101.19, J103.19, J104.19, J105.2, SW_3V3_EN_DIO1.2 (B)
DIO2_5V_EN_FROM_BOSS: J101.20, J103.20, J104.20, J105.5, SW_5V_EN_DIO2.2 (B)
GND: C101.2, D_3V3.1 (K), D_5V0.1 (K), H_GND_1.1, H_GND_2.1, H_GND_3.1, J101.13, J101.14, J102.4, J103.13, J103.14, J104.13, J104.14, J105.3, J105.6, J109.4, J110.5, J110.6, J111.5, J111.6, J_3V3_1.1, J_3V3_2.1, J_5V_1.1, J_5V_2.1, SW_3V3_EN_DIO1.3 (C), SW_5V_EN_DIO2.3 (C), SW_RST1.1
unnamed: D_3V3.2 (A), R_3V3.2
unnamed: D_5V0.2 (A), R_5V0.2
unnamed: J102.3, JP104.2 (B)
unnamed: J102.5, JP105.2 (B)
unnamed: J109.3, JP103.2 (B)
unnamed: J109.5, JP102.2 (B)
unnamed: JP101.2 (C), R101.1, R102.1
unnamed: R102.2, SW_3V3_EN_DIO1.1 (A)
unnamed: R101.2, SW_5V_EN_DIO2.1 (A)
ST_RST: C101.1, J101.3, J103.3, J104.3, J110.1, J111.1, SW_RST1.2
ST_SWDCLK: J101.2, J103.2, J104.2, J110.2, J111.2
ST_SWDIO: J101.1, J103.1, J104.1, J110.4, J111.4
SUP_3V3_1: J101.49, J101.50, J103.49, J103.50, J104.49, J104.50
SUP_3V3_2: H_3V3_1.1, J103.25, J103.26, J104.25, J104.26, J105.1, J105.4, J110.7, J110.8, J111.7, J111.8, JP101.1 (A), JP102.1 (A), JP105.1 (A), JP_3V_SENSE_1.2 (B), J_3V3_1.2, J_3V3_2.2, R_3V3.1
SUP_5V0: H_5V_1.1, J103.15, J103.16, J104.15, J104.16, J110.9, J110.10, J111.9, J111.10, JP101.3 (B), JP103.1 (A), JP104.1 (A), JP_5V_SENSE_1.2 (B), J_5V_1.2, J_5V_2.2, R_5V0.1
SUP_UNREG_1: J101.23, J101.24, J103.23, J103.24, J104.23, J104.24
SUP_UNREG_2: J101.35, J101.36, J103.35, J103.36, J104.35, J104.36

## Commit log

2023-03-26 Add radfet symbol, schematic pages
    [BIRDS-X-PCB.kicad_pcb, BIRDS-X-PCB.kicad_sch, MicrocontrollerSheet.kicad_sch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]
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2023-04-06 Migrate libraries, create LTC4361 symbol
    [BIRDS-X-PCB.kicad_sch, MicrocontrollerSheet.kicad_sch, PowerSheet.kicad_sch]
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2023-04-06 Bug fix
    [Experiment.kicad_sch]
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2023-04-09 Add flash, temperature sensor, etc.
    [BIRDS-X-PCB.kicad_sch, Experiment.kicad_sch, MicrocontrollerSheet.kicad_sch]
2023-04-09 Add BOM and footprints
    [BIRDS-X-PCB.csv, BIRDS-X-PCB.kicad_sch, Experiment.kicad_sch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]
2023-04-11 Added current source circuitry for RADFET Readout
    [Experiment.kicad_sch]
2023-04-12 Completed MCU & Experiment Circuit
    [BIRDS-X-PCB.kicad_sch, Experiment.kicad_sch, MicrocontrollerSheet.kicad_sch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]
2023-04-12 Fixed voltage dividers
    [Experiment.kicad_sch]
2023-04-13 Add TODO and update PDF
    [Experiment.kicad_sch]
2023-04-15 Added RFET enabling connections
    [BIRDS-X-PCB.csv, BIRDS-X-PCB.kicad_sch, Experiment.kicad_sch]
2023-04-16 Semantic and symbol updates, begin review changes
    [BIRDS-X-PCB.kicad_sch, Experiment.kicad_sch, MicrocontrollerSheet.kicad_sch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]
2023-04-16 MCU pin assignment review
    [BIRDS-X-PCB.kicad_sch, MicrocontrollerSheet.kicad_sch]
2023-04-16 Add more MCU changes
    [BIRDS-X-PCB.kicad_sch, Experiment.kicad_sch, MicrocontrollerSheet.kicad_sch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]
2023-04-16 Implement oscillator improvements
    [BIRDS-X-PCB.kicad_sch, Experiment.kicad_sch, MicrocontrollerSheet.kicad_sch]
2023-04-16 Add logic level converters, etc.
    [Experiment.kicad_sch, MicrocontrollerSheet.kicad_sch]
2023-04-16 Fix power enable issue
    [BIRDS-X-PCB.kicad_sch, MicrocontrollerSheet.kicad_sch, PowerSheet.kicad_sch]
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2023-04-16 Add core restricted layouts and lock them
    [BIRDS-X-PCB.csv, BIRDS-X-PCB.kicad_pcb, BIRDS-X-PCB.kicad_sch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]
2023-04-16 Fix flash signals, fix footprints
    [BIRDS-X-PCB.csv, BIRDS-X-PCB.kicad_pcb, BIRDS-X-PCB.kicad_sch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]
2023-04-20 Add notes from schematic review session
    [BIRDS-X-PCB.kicad_pcb, Experiment.kicad_sch, MicrocontrollerSheet.kicad_sch]
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2023-04-22 Update tempo current source
    [Experiment.kicad_sch, MicrocontrollerSheet.kicad_sch]
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2023-04-22 Route more, move MCU
    [BIRDS-X-PCB.kicad_pcb]
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2023-04-23 Fix DRC issues
    [BIRDS-X-PCB.kicad_pcb]
2023-04-23 Finish fixing DRC issues, except power lines
    [BIRDS-X-PCB.kicad_pcb]
2023-04-23 Route power lines on 2-layer board, if desired
    [BIRDS-X-PCB.kicad_pcb, MicrocontrollerSheet.kicad_sch]
2023-04-23 Minor layout changes to consolodate ground planes
    [BIRDS-X-PCB.kicad_pcb, Experiment.kicad_sch]
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2023-04-23 Move 3v3 and 5v lines to polygon pour layers
    [BIRDS-X-PCB.kicad_pcb]
2023-04-23 Re-route power lines from input to protection
    [BIRDS-X-PCB.kicad_pcb, PowerSheet.kicad_sch]
2023-04-28 Update resistor vals, plot, BOM
    [BIRDS-X-PCB.csv, BIRDS-X-PCB.kicad_pcb, BIRDS-X-PCB.kicad_sch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]
2023-04-28 Update copper anulus on mounting holes
    [BIRDS-X-PCB.kicad_pcb]
2023-04-28 Add logos and final labels
    [BIRDS-X-PCB.kicad_pcb]
2023-04-29 Final changes for rev1
    [BIRDS-X-PCB.csv, BIRDS-X-PCB.kicad_pcb, MicrocontrollerSheet.kicad_sch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]
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2023-04-29 Add text silk screen areas
    [BIRDS-X-PCB-B_Cu.gbl, BIRDS-X-PCB-B_Mask.gbs, BIRDS-X-PCB-B_Paste.gbp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]
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2023-05-28 Remove all Rev1.0 gerbers
    [BIRDS-X-PCB-B_Cu.gbl, BIRDS-X-PCB-B_Mask.gbs, BIRDS-X-PCB-B_Paste.gbp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]
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2023-06-13 Add PIN Diode experiment
    [BIRDS-X-PCB.kicad_sch, PINDiodeExperiment.kicad_sch]
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2023-06-13 Update footprints to 0603
    [BIRDS-X-PCB.kicad_pcb, MicrocontrollerSheet.kicad_sch, PINDiodeExperiment.kicad_sch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]
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2023-06-13 Re-organize PIN diode sheet structure
    [BIRDS-X-PCB.kicad_pcb, BIRDS-X-PCB.kicad_sch, PINDiodeExperiment.kicad_sch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]
2023-06-13 Continue layout and routing
    [BIRDS-X-PCB.kicad_pcb]
2023-06-14 Add MCU assignments, RF annotations per ref design, heirarchal pins
    [BIRDS-X-PCB.kicad_sch, MicrocontrollerSheet.kicad_sch, PINDiodeExperiment.kicad_sch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]
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2023-06-16 Move around silkscreens for final production
    [BIRDS-X-PCB.kicad_pcb, BIRDS-X-PCB.kicad_sch, RadfetExperiment.kicad_sch]
2023-06-16 Add EMC protection for 12V step-up
    [BIRDS-X-PCB.kicad_pcb, PINDiodeExperiment.kicad_sch, PowerSheet.kicad_sch]
2023-06-16 Add semi-random radiation shielding mounting holes
    [BIRDS-X-PCB.kicad_pcb, BIRDS-X-PCB.kicad_sch]
2023-06-20 Update pins and LCSC part numbers
    [MicrocontrollerSheet.kicad_sch, PINDiodeExperiment.kicad_sch, RF_System.kicad_sch]
2023-06-21 Add final Rev2 production files
    [bom.csv, designators.csv, positions.csv]
2023-06-22 Add LCSC LM334 part number for next time, remove point-in-time files
    [BIRDS-X-PCB.csv, PINDiodeExperiment.kicad_sch, RadfetExperiment.kicad_sch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]
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2023-07-21 Add NucleoTNC schematic copy
    [PINDiodeExperiment.kicad_sch, RF_System.kicad_sch]
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2023-07-21 Update parts in RF system
    [RF_System.kicad_sch]
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2023-07-23 Finish double MCU re-org
    [BIRDS-X-PCB.kicad_sch, MicrocontrollerSheet.kicad_sch, RF_System.kicad_sch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]
2023-07-23 Restore old microcontroller setup
    [MicrocontrollerSheet.kicad_sch]
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2023-07-24 Finish MCU pin assignments for UART/I2C
    [MicrocontrollerSheet.kicad_sch, RF_System.kicad_sch]
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2023-07-24 Assign remaining footprints, fix Annotations
    [BIRDS-X-PCB.kicad_sch, RF_System.kicad_sch, RF_System_MCU.kicad_sch]
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2023-07-24 Do most of routing
    [BIRDS-X-PCB.kicad_pcb, BIRDS-X-PCB.kicad_sch, MicrocontrollerSheet.kicad_sch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]
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2023-07-24 Fix all DRC
    [BIRDS-X-PCB.kicad_pcb, BIRDS-X-PCB.kicad_sch, PowerSheet.kicad_sch]
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2023-07-24 Add rev3 JLC production files
    [BIRDS-X-PCB-B_Cu.gbl, BIRDS-X-PCB-B_Mask.gbs, BIRDS-X-PCB-B_Paste.gbp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]
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2023-08-22 Start test fixture PCB
    [BIRDS-X-Test-Fixture-PCB.kicad_pcb, BIRDS-X-Test-Fixture-PCB.kicad_sch]
2023-08-22 Done test fixture schematic
    [BIRDS-X-Test-Fixture-PCB.kicad_sch]
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2023-08-22 Finish test fixture
    [BIRDS-X-Test-Fixture-PCB.kicad_pcb, BIRDS-X-Test-Fixture-PCB.kicad_sch, bom.csv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]
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2023-08-22 Update labels on test fixture
    [BIRDS-X-Test-Fixture-PCB.kicad_pcb]
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2023-08-22 Fix logo
    [BIRDS-X-PCB.kicad_pcb, BIRDS-X-PCB.kicad_sch]
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2023-08-23 Revert "Bigger welp"
    This reverts commit 0054a0e7b2f6f9c4b8ea2502b56168c89fe4c559.
    [BIRDS-X-PCB.kicad_pcb]
2023-08-23 Revert "Welp"
    This reverts commit 5da3a1a40cdef91cfc9ebce7a6f18400f4c29f94.
    [BIRDS-X-PCB.kicad_pcb]
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2023-08-24 Fix missing connections, release Rev5.0
    [BIRDS-X-PCB.kicad_sch, MicrocontrollerSheet.kicad_sch, PINDiodeExperiment.kicad_sch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]
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2023-11-13 Minor DRC fixes
    [BIRDS-X-PCB.kicad_pcb]
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2023-11-27 Fix up broken bits
    [BIRDS-X-PCB.kicad_pcb]
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2023-11-29 Schematic re-work (esp. RADFET fixes)
    [BIRDS-X-PCB.kicad_sch, LinearCCD.kicad_sch, MicrocontrollerSheet.kicad_sch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]
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2023-11-30 Fix BJT on CCD circuit
    [BIRDS-X-PCB.kicad_pcb, LinearCCD.kicad_sch, RadfetExperiment.kicad_sch]
2023-11-30 Update test fixture board
    [BIRDS-X-Test-Fixture-PCB.kicad_pcb, BIRDS-X-Test-Fixture-PCB.kicad_sch]
2023-11-30 Finish routing test fixture board
    [BIRDS-X-Test-Fixture-PCB.kicad_pcb]
2023-11-30 Touch up test fixture board
    [BIRDS-X-Test-Fixture-PCB.kicad_pcb, BIRDS-X-Test-Fixture-PCB.kicad_sch]
2023-11-30 Generate test fixture gerber
    [BIRDS-X-Test-Fixture-PCB.kicad_pcb, bom.csv, designators.csv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]
2023-11-30 Update test fixture schematic PDF
    [BIRDS-X-Test-Fixture-PCB.kicad_pcb]
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2023-12-03 Set hidden state on header pins in render
    [BIRDS-X-PCB.kicad_pcb]
2023-12-14 Test fixture - update resistor values, add stand offs
    [BIRDS-X-Test-Fixture-PCB.kicad_sch, pcb_stand_off.scad, pcb_stand_off.stl]
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
